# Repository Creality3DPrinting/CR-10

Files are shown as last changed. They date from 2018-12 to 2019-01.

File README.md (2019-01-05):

# CR-10
The original, large build area, all-metal 3D printer from Creality3D is now fully Open Source Hardware Association Certified.

UID:CN000005
https://certification.oshwa.org/list.html

Hardware and software licensed under the GPL v3 license, documentation licensed under CC BY-SA 4.0 International license.

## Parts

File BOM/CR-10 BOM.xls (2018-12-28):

CR-10 BOM
order | Part Code | Part Name | Specification | UNIT | Qty
1 | 400102047 | 2020-L400-X-1 | 20*20-L400 | PCS | 2
2 | 400102015 | 2040-L460-A0-1 | 20*40-L460mm | PCS | 2
3 | 400102048 | 2040-L500-A0-1 | 20*40-L509 | PCS | 1
4 | 400101026 | Y Motor holder 1 | 2.5mmSPCC | PCS | 1
5 | 400205046 | M5X10 Pan Head Screw | M5X10 | PCS | 3
6 | 400202005 | F624 pillow | F624zz | PCS | 4
7 | 400205102 | M5 T-Slot Nut | M5TNUT | PCS | 1
8 | 400205052 | M5X25Socket Head Screw | M5X25 | PCS | 16
9 | 400205107 | M5 Split Washer | M5 | PCS | 1
10 | 200101010 | Hot bed control module |  | PCS | 1
11 | 400101108 | Y Adjustment Block-1 | 2.0mm | PCS | 1
12 | 400408004 | M4X15 Hollow cylinder | 4.2*8*15mm | PCS | 2
13 | 400205012 | M4X50 Sock Head Screw | M4X50 | PCS | 1
14 | 400205137 | M5X30 Socket Head Screw | M5*30 | PCS | 4
15 | 400101025 | Side Plate | 4mmAL5052 | PCS | 1
16 | 400302016 | Hot bed-1 | 310*310*3-220W | PCS | 1
17 | 400505003 | Glass platform | 310*310*4mm | PCS | 1
18 | 400205141 | M4X18-P Flush Head Screw | M4X18-P | PCS | 21
19 | 400205096 | M4 Self-locking nut | M4 | PCS | 1
20 | 400404029 | Y limit switch bracket-1 | 4mm | PCS | 1
21 | 400101016 | Fan holder | 0.8mm | PCS | 1
22 | 400205063 | M3X25-P | M3X25-P | PCS | 4
23 | 400205028 | M3X4 Pan Head Screw | M3*5 | PCS | 9
24 | 400309008 | 4025Fan | 12V-4020-0.12A | PCS | 1
25 | 400305014 | Power supply socket |  | PCS | 1
26 | 200102008 | lcd | 12864 | PCS | 1
27 | 400307001 | lcd Knob |  | PCS | 1
28 | 200101004 | CR-10 Control Panel | Melzi | PCS | 1
29 | 400205134 | M3X18 Combination Screw | M3*18 | PCS | 4
30 | 400205030 | M3X8 Pan Head Screw | M3X8 | PCS | 4
31 | 400309007 | 5010 Fan | 12V-5010-0.12A | PCS | 1
32 | 400205104 | M30 Plastic nut | M30*1.5 | PCS | 2
33 | 400403001 | Support tube | D32-L100 | PCS | 1
34 | 400205088 | M3X6 Hand Twisted Screw | M3*6 | PCS | 2
35 | 400205037 | M4X6 Pan Head Screw | M4X6 | PCS | 4
36 | 400301004 | Power Supply | INPUT:100/220VOUTPUT:12V30A | PCS | 1
37 | 400305013 | Switch |  | PCS | 1
38 | 400102052 | 2040-L550-A0-1 | 20*40-L550 | PCS | 1
39 | 400102064 | 2040-L550-A0-1 | 20*40-L550 | PCS | 1
40 | 400201001 | 42-34 motor | JK42HS34-0844YA-03F | PCS | 1
41 | 400402010 | Z motor bracket |  | PCS | 1
42 | 400208001 | Z coupler | CI-20X26-5X8 | PCS | 1
43 | 400205140 | M3X40-P | M3X10-P | PCS | 4
44 | 400102020 | 2020-L400-A0-1 | 20*20-L400mm | PCS | 1
45 | 400102054 | 2020-L415-A0-1 | 20*20-L415mm | PCS | 1
46 | 400101029 | Fan cover | 0.8mmSPOCC | PCS | 1
47 | 400309005 | Nozzle fan | 12V-4010-0.07A-L1200-N5800 | PCS | 1
48 | 400309006 | Cold section fan | 12V-4010-0.2A，L1200 | PCS | 1
49 | 400402023 | Nozzle fan duct |  | PCS | 1
50 | 400205002 | M2X8 Socket Head Screw | M2X8 | PCS | 2
51 | 400205003 | M2X10 Socket Head Screw | M2X10 | PCS | 2
52 | 400101027 | Z Stent | 3.0mm | PCS | 1
53 | 400402021 | Z Threaded Rod Holder-A |  | PCS | 1
54 | 400402022 | Z Threaded Rod Holder-B |  | PCS | 1
55 | 400205042 | M4X20 Pan Head Screw | M4X20 | PCS | 2
56 | 400205061 | M3X14 Flush Head Screw | M3*14-P | PCS | 2
57 | 400101006 | X Adjustment Block | 3mm | PCS | 1
58 | 400205057 | M8X25 Pan Head Screw | M8X25 | PCS | 1
59 | 400205093 | M8 nut | M8Nut | PCS | 1
60 | 400202003 | F688 pillow | F688 | PCS | 3
61 | 400205098 | M8 Self-locking nut | M8Nut | PCS | 1
62 | 400205013 | M4X8 Socket Head Screw | M4X8 | PCS | 3
63 | 400205101 | M4 T-Slot Nut | M4TNut | PCS | 5
64 | 400101103 | E motor bracket | 2.5mmAL5052 | PCS | 1
65 | 400101104 | X motor bracket | 3mmAL5052 | PCS | 1
66 | 400205055 | M5X40 Pan Head Screw | M5X40 | PCS | 3
67 | 400108001 | Spacers for rollers | D8-d5-H-8.35mm | PCS | 12
68 | 400403003 | Rollers | D16 | PCS | 15
69 | 400205110 | M5 washer1 | M5*8*1 | PCS | 15
70 | 400202004 | 625pillow | 625 | PCS | 30
71 | 400205097 | M5 Self-locking nut | M5Nut | PCS | 15
72 | 400201004 | 40-42 motor | JK42HS40-1004AC-01F | PCS | 3
73 | 400402027 | E housing |  | PCS | 1
74 | 400205031 | M3X10 Pan Head Screw | M3X10 | PCS | 8
75 | 400205060 | M3X10 Flush Head Screw | M3X10-P | PCS | 1
76 | 400402026 | E idler tensioner |  | PCS | 1
77 | 400205007 | M3X18 Socket Head Screw | M3X18 | PCS | 1
78 | 400202002 | 624U pillow | 624U | PCS | 1
79 | 400205111 | z nut | T8*8 | PCS | 1
80 | 400205106 | M4 Split Washer | M4 | PCS | 5
81 | 400205105 | M3 Split Washer | M3 | PCS | 6
82 | 400304001 | limit switch | 3PIN | PCS | 3
83 | 400103001 | E gear | D11-40 | PCS | 1
84 | 400204002 | Extrusion Spring | 1.1*外8*L22 | PCS | 1
85 | 400210002 | M6 Pneumatic joint | KJH04-06 | PCS | 1
86 | 400211001 | 2GT-pulley | 2GT-d5-20-6mm | PCS | 2
87 | 400404038 | X limit switch bracket |  | PCS | 1
88 | 400205029 | M3X6Pan Head Screw | M3X6 | PCS | 18
89 | 400108002 | Eccentric column | D7.2-d5-H-8.35mm | PCS | 6
90 | 400202148 | M4X16 Pan Head Screw | M4X16 | PCS | 2
91 | 400101002 | E plate | 2.5mmAL5052 | PCS | 1
92 | 400205053 | M5X30 Pan Head Screw | M5X30 | PCS | 12
93 | 400205109 | M5 washer | M5 | PCS | 5
94 | 400205041 | M4X16 Pan Head Screw | M4X16 | PCS | 2
95 | 400205015 | M4X16 Screw | M4*16 | PCS | 2
96 | 400105008 | Radiator | 12*20*27.8mm,2*M3 | PCS | 1
97 | 400107006 | Catheter | D7*M6-L27mm | PCS | 1
98 | 400104004 | Heat block | 20*20*10 | PCS | 1
99 | 400106003 | nozzle | D6-0.4mm | PCS | 1
100 | 400205018 | M3 Screw | M3X3 | PCS | 2
101 | 400308005 | Heater | 12V，40W-L1200mm，Φ6*20 | PCS | 1
102 | 400303008 | Nozzle thermistor | D1.8-L1200mm-100K | PCS | 1
103 | 400205021 | M3X4 Screw | M3X4 | PCS | 1
104 | 400210001 | Pneumatic joint | D4M8 | PCS | 1
105 | 400407003 | D4 Teflon tube | D4-d2-L440mm | PCS | 1
106 | 400205007 | M3×18 Flush Head Screw | M3×25 | PCS | 2
107 | 400205032 | M3X16 Pan Head Screw | M3X16 | PCS | 4
108 | 400204001 | Bed level springs | 0.9*8*L17 | PCS | 4
109 | 400205066 | M4X30 Flush Head Screw | M4*30-P | PCS | 4
110 | 400205164 | Hand Twisted Nut | M4-D60 | PCS | 4
111 | 400402020 | 2020 Endcap | 2020 | PCS | 6
112 | 400404035 | Connecting Block | 40*55*5 | PCS | 4
113 | 400406005 | Foot Cushion | D25*3mm | PCS | 4
114 | 400205039 | M4X10 Pan Head Screw | M4X10 | PCS | 1
115 | 400101030 | Casing | 0.8mmSPCC | PCS | 1
116 | 400101032 | Sipport Frame1 | 1.5mmSPCC | PCS | 1
117 | 400101127 | Bottom cover | 0.8mmSPCC | PCS | 1
118 | 400404037 | T-jiont plates | 5mm | PCS | 1
119 | 400404036 | T-jiont plates | 5mm | PCS | 1
120 | 400206001 | Z threaded rod-514 | D8-T8*8-L515mm | PCS | 1
121 | 400205015 | M4X16 Sochet Head Screw | M4*16 | PCS | 1
122 | 400306225 | Y Motor Line | L420mm | PCS | 1
123 | 400306226 | Z Motor Line | Motor LineL280mm，Limit Line L180mm | PCS | 1
124 | 400306069 | Display line | 10pin,L190mm | PCS | 1
125 | 400306121 | power line | 16#-L200mm,XT60 | PCS | 1
126 | 400306124 | Red silicone wire | 16#-L200mm | PCS | 1
127 | 400306125 | Red silicone wire | 16#-L150mm | PCS | 1
128 | 400306127 | Red silicone wire | 16#-L170mm | PCS | 1
129 | 400306128 | Yellow silicone wire | 18#-L170mm | PCS | 1
130 | 400306144 | Black silicone wire | 16#-L200mm | PCS | 1
131 | 400306145 | Black silicone wire | 16#-L170mm | PCS | 1
132 | 400306147 | Red silicone wire | 16#-L100mm | PCS | 1
133 | 400306148 | Black silicone wire | 16#-L100mm | PCS | 1
134 | 400306151 | X,E Motor Line | Motor Line L860mm、980mm，Limit Line L920mm | PCS | 1
135 | 400306152 | Y Motor Line | Motor Line L860mm，Limit Line L780mm | PCS | 1
136 | 400306153 | Z Motor Line | Motor Line L860mm，Limit Line L780mm | PCS | 1
137 | 400306234 | aviation connector-8 |  | PCS | 1
138 | 400306235 | aviation connector-8 |  | PCS | 1

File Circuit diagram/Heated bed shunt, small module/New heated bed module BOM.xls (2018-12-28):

 | 新热床模块BOM单
序号 | 名称 | 物料规格 | 位置 | 封装 | 单位 | 单位用量
1 | 连接器 | 2PIN 2.54间距米色座子 | Control In | XH2.54-2A | PCS | 1
2 | LED | 蓝色LED灯 | D1, D2 | 0805 | PCS | 2
3 | 场效应管 | HA210N10 | Q2 | TO-247 | PCS | 1
4 | 电阻 | 2K ±1% 1/8W | R1, R3 | 0805 | PCS | 2
5 | 电阻 | 10K ±1% 1/8W | R2, R4, R5 | 0805 | PCS | 3
6 | 整流桥堆 | MP6S 整流桥堆 600V/0.5A | U1 | SOP-4 | PCS | 1
7 | 连接器 | 7.62mm间距 3PIN 连接器 | U2 | KF7.62-3P | PCS | 1
8 | 光电耦合器 | PC817 光电耦合器 | U3 | SOP-4 | PCS | 1

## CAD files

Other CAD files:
3D/CR-10.sldasm
3D/CR-10_1.sldasm
2D/E motor bracket.dwg
2D/Fan holder.DWG
2D/Rollers.dwg
2D/Z Threaded Rod Holder-A.DWG
2D/Support Frame.DWG
2D/Bottom cover.DWG
2D/Glass platform.DWG
2D/Y limit switch bracket.DWG
2D/2040-L460-A0-1.DWG
2D/X limit switch bracket.DWG
2D/Heat block.dwg
2D/2020-L415-A0-1.DWG
2D/Y Motor holder.DWG
2D/E housing.dwg
2D/Y Adjustment Block.DWG
2D/Fan cover.dwg
2D/2020 Endcap.dwg
2D/2020-L400-A0-1.DWG
2D/2040-L500-A0-1.DWG
2D/Casing.DWG
2D/Catheter.dwg
2D/E idler tensioner.dwg
2D/E plate.dwg
2D/Eccentric column.dwg
2D/Foot Cushion.DWG
2D/Hand Twisted Nut.dwg
2D/M30 Plastic nut.dwg
2D/Nozzle fan duct.dwg
2D/Radiator.dwg
2D/Side Plate.DWG
2D/Spacers for rollers.dwg
2D/Support tube.dwg
2D/T-jiont plates-2.DWG
2D/T-jiont plates.DWG
2D/X Adjustment Block.dwg
2D/X motor bracket.dwg
2D/Z Stent.dwg
2D/Z Threaded Rod Holder-B.DWG
2D/Z motor bracket.dwg
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

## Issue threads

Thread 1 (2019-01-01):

CR-10 Schematic.pdf does not match CR-10 Motherboard.PCB

RudolphRiedel, 2019-01-01:
Thank you for making all this available!
I just found out about it, this would probably have stopped me from doing my own version.

But the provided CR-10 Schematic.pdf does not match CR-10 Motherboard.PCB.
The part names are all wrong, the controller is named U5 in your schematic but named U8 on the board.
I have not found a single part yet that has the same name in your CR-10 Schematic.pdf  as in your CR-10 Motherboard.PCB.
Also the values for the components do not match and some values are even missing.
And some of the signal names to do not match as well.

Please do provide a schematic that matches the board file.
And please do consider providing the schematic in binary form as well as placement plan in .pdf for the board.

RudolphRiedel, 2019-01-12:
The header J5 clearly shows that the provided "CR-10 Schematic.pdf" is not for the V1.1.2 version of the board but for the earlier revision that did not have a revision printed on the silkscreen.
The V1.1.2 board does not have the jumper to switch 5V from VREG_5V to USB.

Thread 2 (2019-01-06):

Values missing for components in Power section of the Schematics

CurtisLeeBolin, 2019-01-06:
Circuit diagram/Motherboard/CR-10 Schematic.pdf

In the Power section, I only see a value for the integrated circuit, an inductor, and the fuse.  No values are given for the other components.  Also the inductor is not numbered.  It is still labeled "L?".

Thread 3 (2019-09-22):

Missing files for electrical components

spermman, 2019-09-22:
I saw a post that made it sound like at one time the models for the board, power supply and display were available.

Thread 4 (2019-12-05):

CR-20 Files and 3D Assembly

amv101, 2019-12-05:
Thanks for making these files available! Great work!

Any chance we can get CR-20 / CR-20 Pro 3D Assembly and PCB schematic files? It seems it is almost identical to the Ender 3, with the exception of the bottom frame housing and mainboard parts.

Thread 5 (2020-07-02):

8-Pin Aviation connector Pinout is incorrect

edumaker-limited, 2020-07-02:
Hi, here is an erratum for the file:
400306234-aviation connector-8-Model.pdf

The PDF states:
1. 1#2# Heater
2. 3#4# Nozzle thermistor
3. 5#nozzle fan (rad), 6#nozzle fan (black)
4. 7#cold section fan(rad); 8#cold section fan(blac).

This is incorrect - the fans are swapped around.  My source:  I own 15 CR10 variants from original to 10s to 10S5, all are the same, and do not match this document.

Here is a suggested correction including spelling and more commonly heard English terminology for the parts:

1. 1#2# Heater
2. 3#4# Nozzle thermistor
3. 5# Heat-sink fan (red); 6#Heat-sink fan (black)
4. 5# part cooling fan (red); 6# part cooling fan (black)

Kind regards,
Alex Gibson
Edumaker Limited

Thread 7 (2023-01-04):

missing Data: X-Carriage & Hotend-Assembly of CR-10 V2 Version

ij0n, 2023-01-04:
I have a CR10-V2. The X-Carriage and Hotend-Assembly does not match the data provided here. I have furthermore added a BL-Touch to that setup. I'd like to have the 3D-Data to design additional attachments for the X-Carriage.

Can you please upload that data?

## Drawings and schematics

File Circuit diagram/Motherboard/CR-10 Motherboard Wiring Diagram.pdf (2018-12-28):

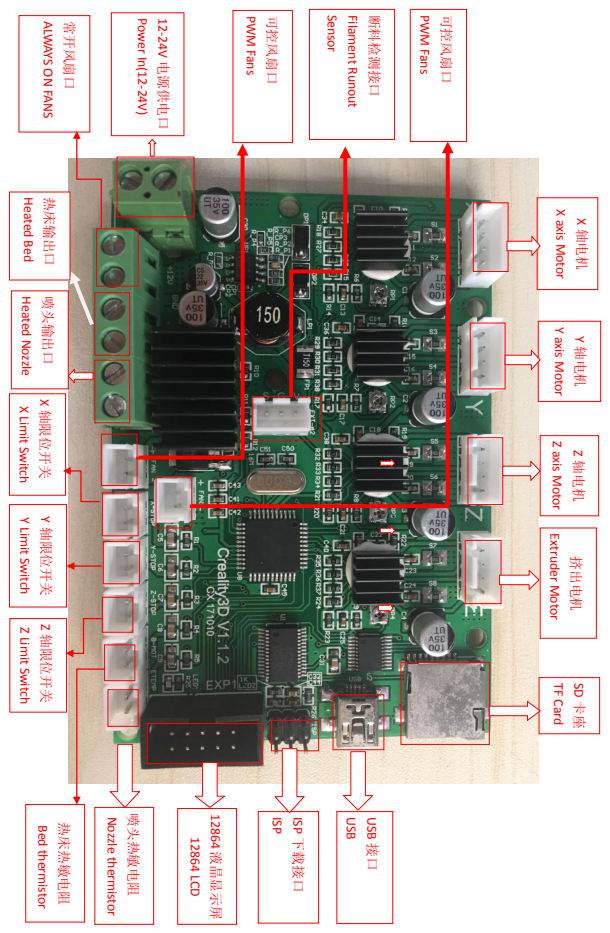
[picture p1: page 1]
Z 轴限位开关; Z Limit Switch; Y 轴限位开关; Y Limit Switch; Z 轴电机; Z axis Motor; USB; 12-24V 电源供电口; Power In(12-24V); 热床输出口; 喷头输出口; Nozzle; PWM; 可控风扇口; Fans; 常开风扇口; 喷头热敏电阻; thermistor; 热床热敏电阻; Bed thermistor; 12864液晶显示屏; 12864 LCD; 轴限位开关 Y 轴限位开关; X Limit Switch; 轴限位开关; Y 轴电机; Y axis Motor; 挤出电机; Extruder Motor; ISP 下载接口; ISP; Filament; 断料检测接口; Runout; Sensor

ALWAYS ON FANS

eated Bed Heated

X Z X 轴电机 X axis Motor SD 卡座 TF Card USB 接口

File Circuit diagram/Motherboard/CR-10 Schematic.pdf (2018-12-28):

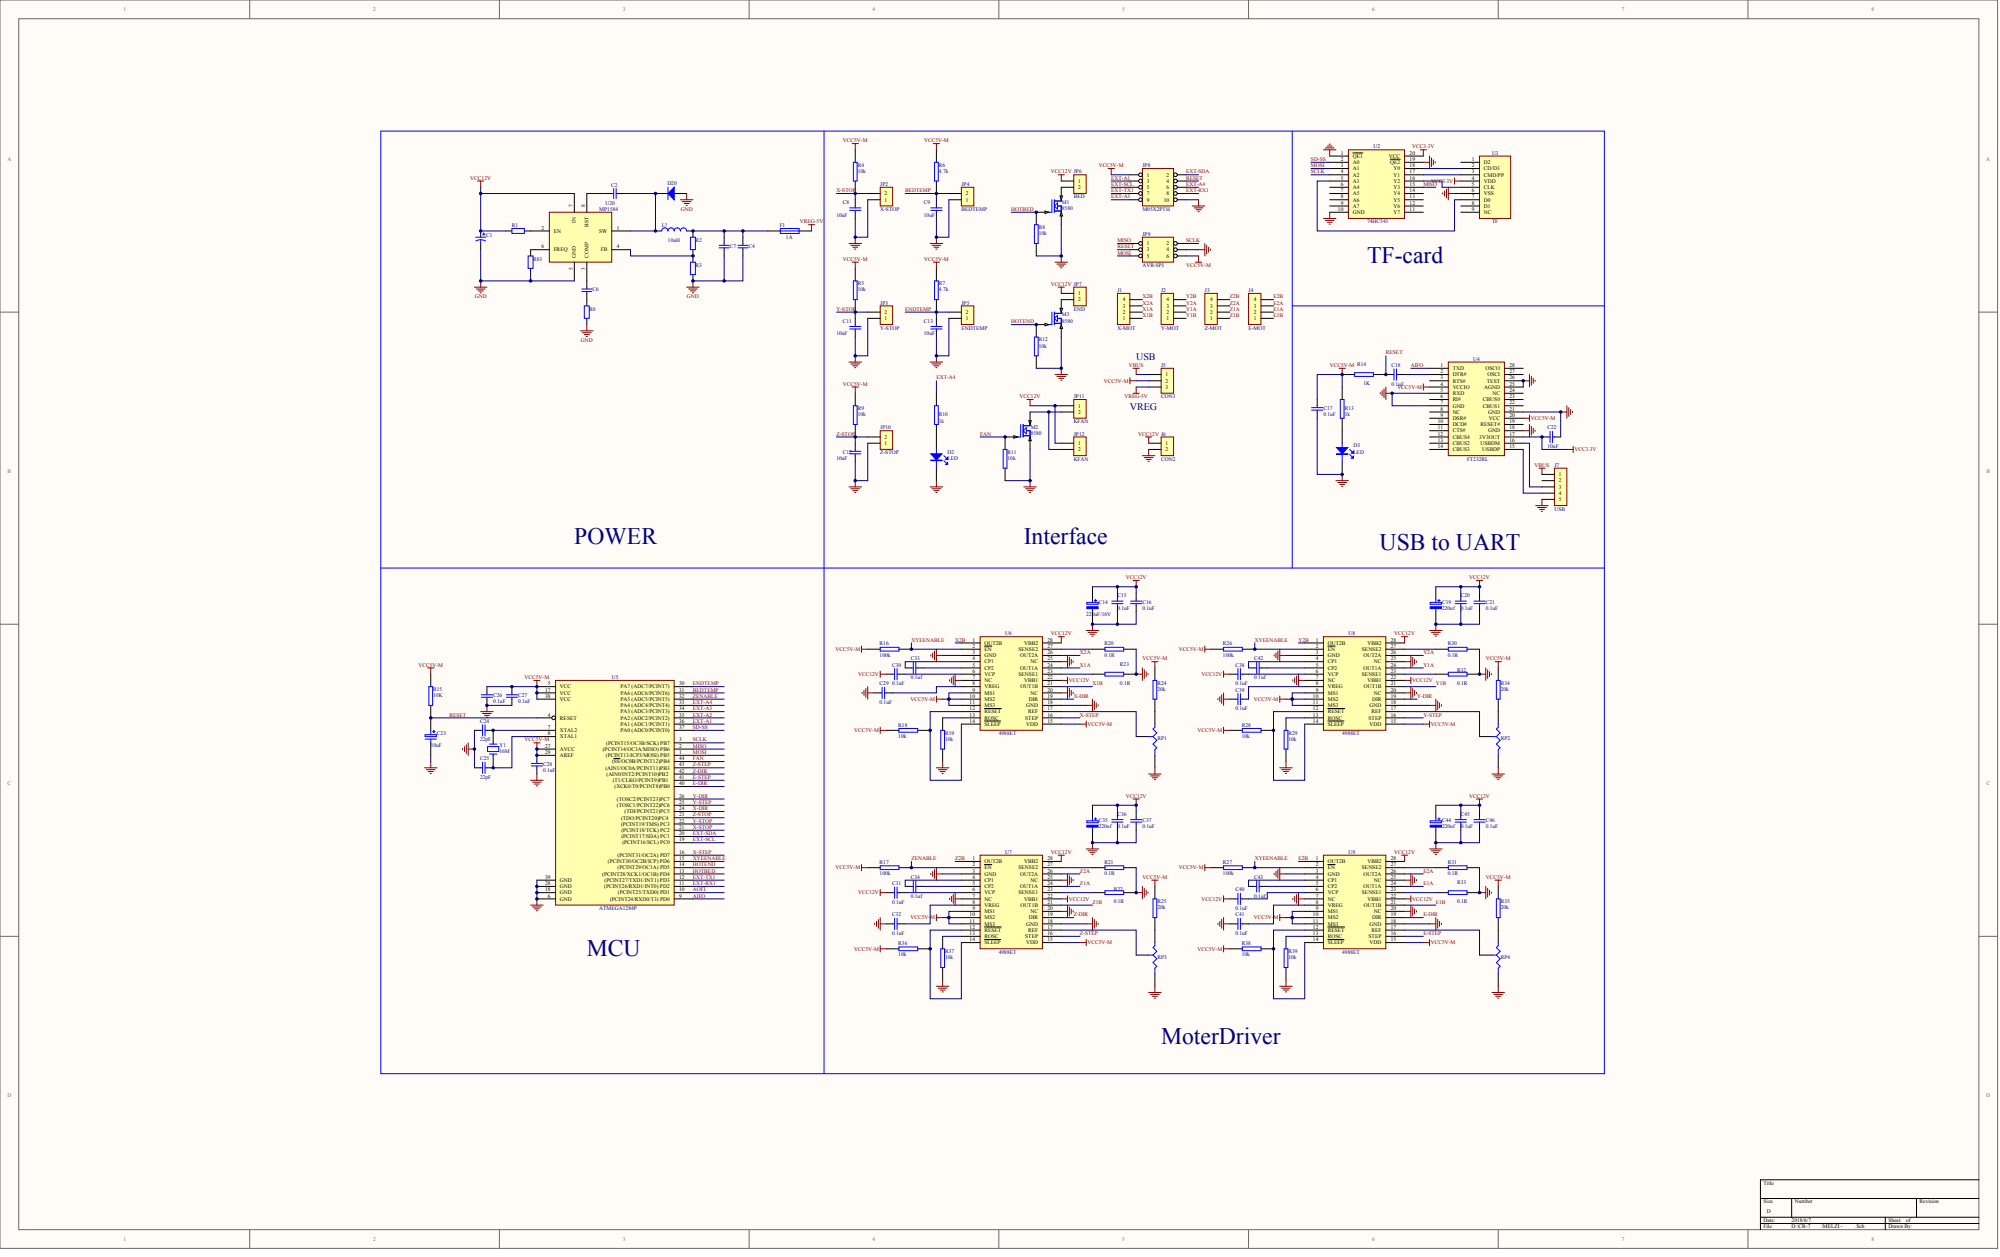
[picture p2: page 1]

DCD# 10 P0U4019 P0U4019 P0U4019
CTS# 11 | P0U4018 P0U4018 P0U4018

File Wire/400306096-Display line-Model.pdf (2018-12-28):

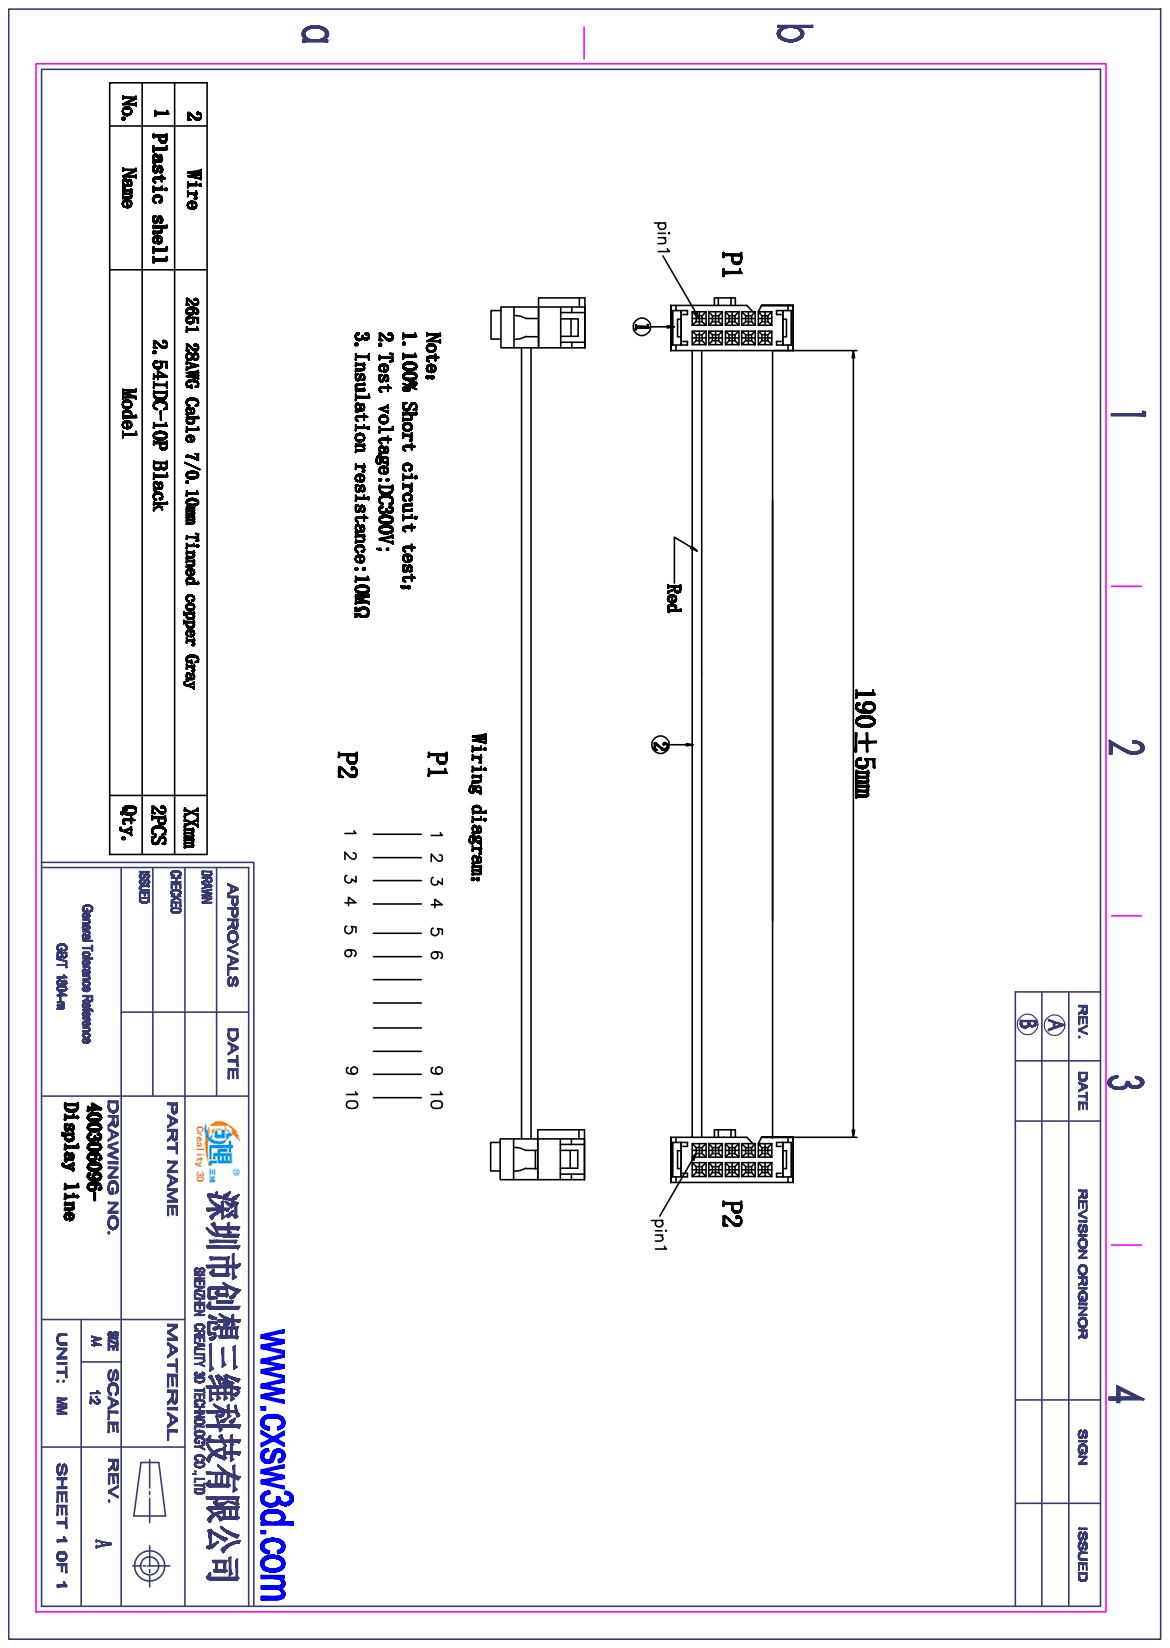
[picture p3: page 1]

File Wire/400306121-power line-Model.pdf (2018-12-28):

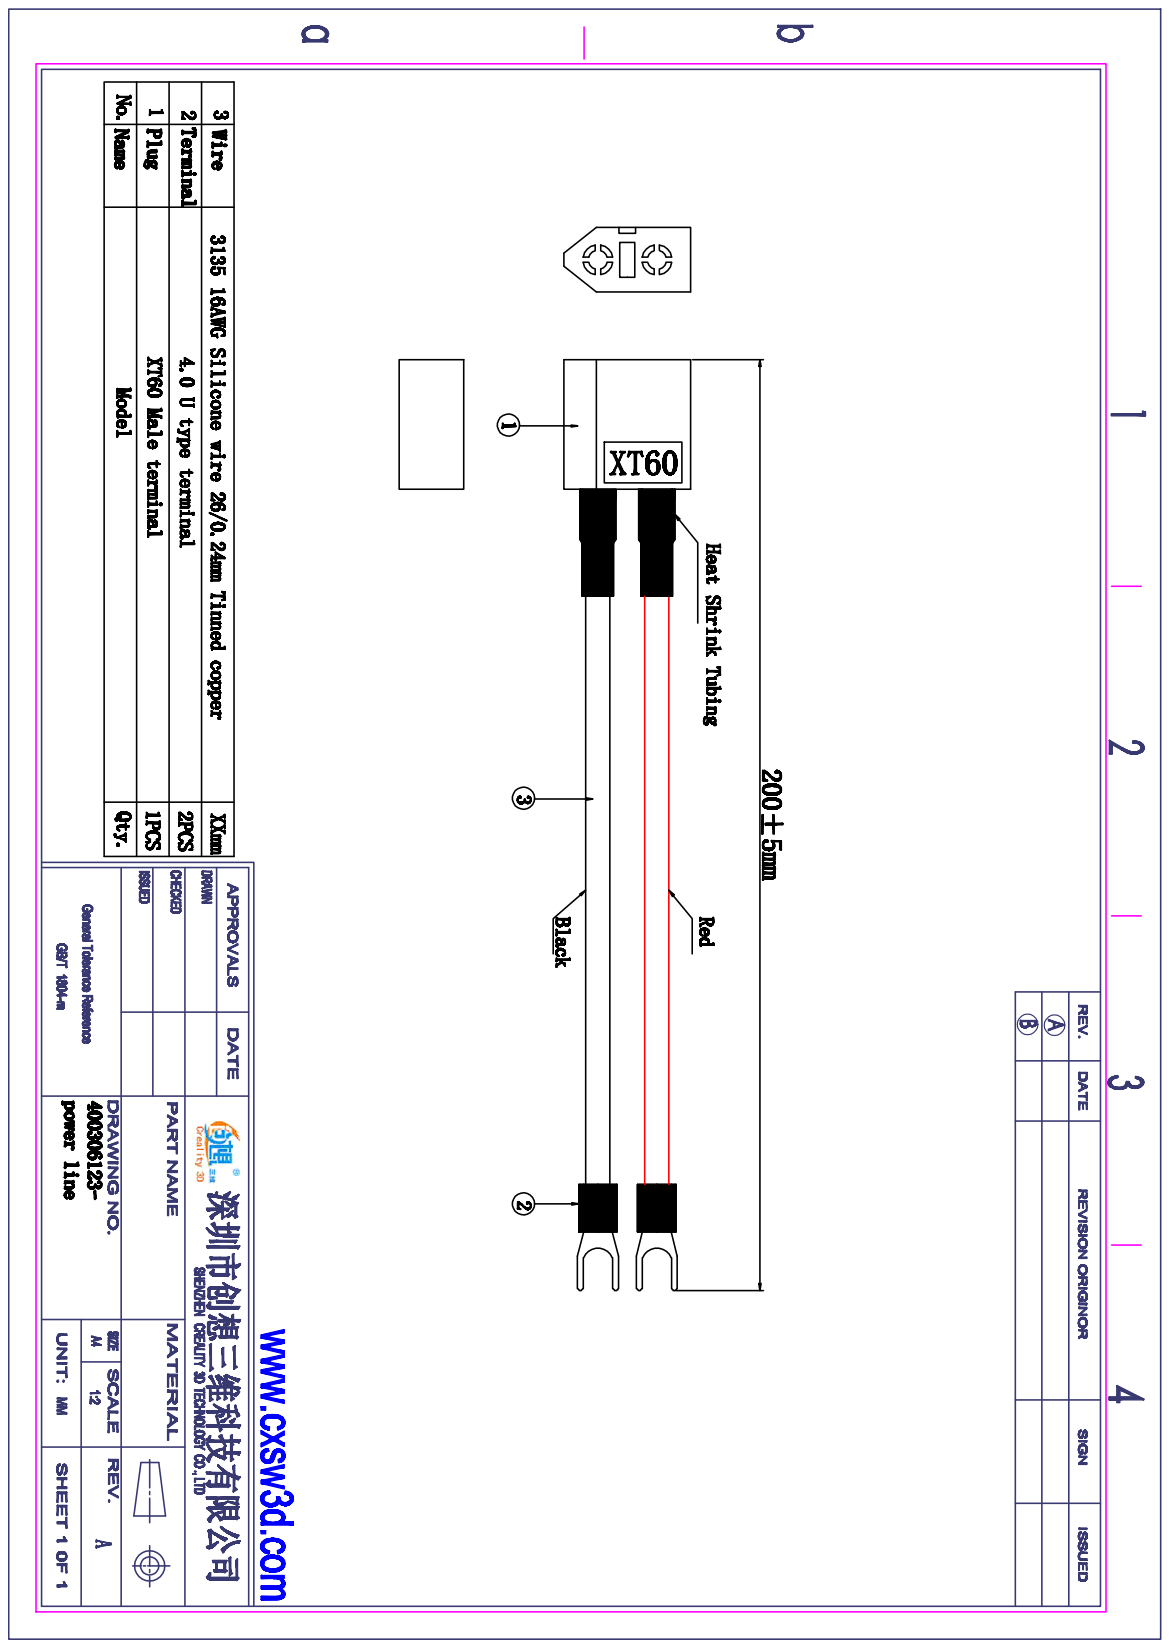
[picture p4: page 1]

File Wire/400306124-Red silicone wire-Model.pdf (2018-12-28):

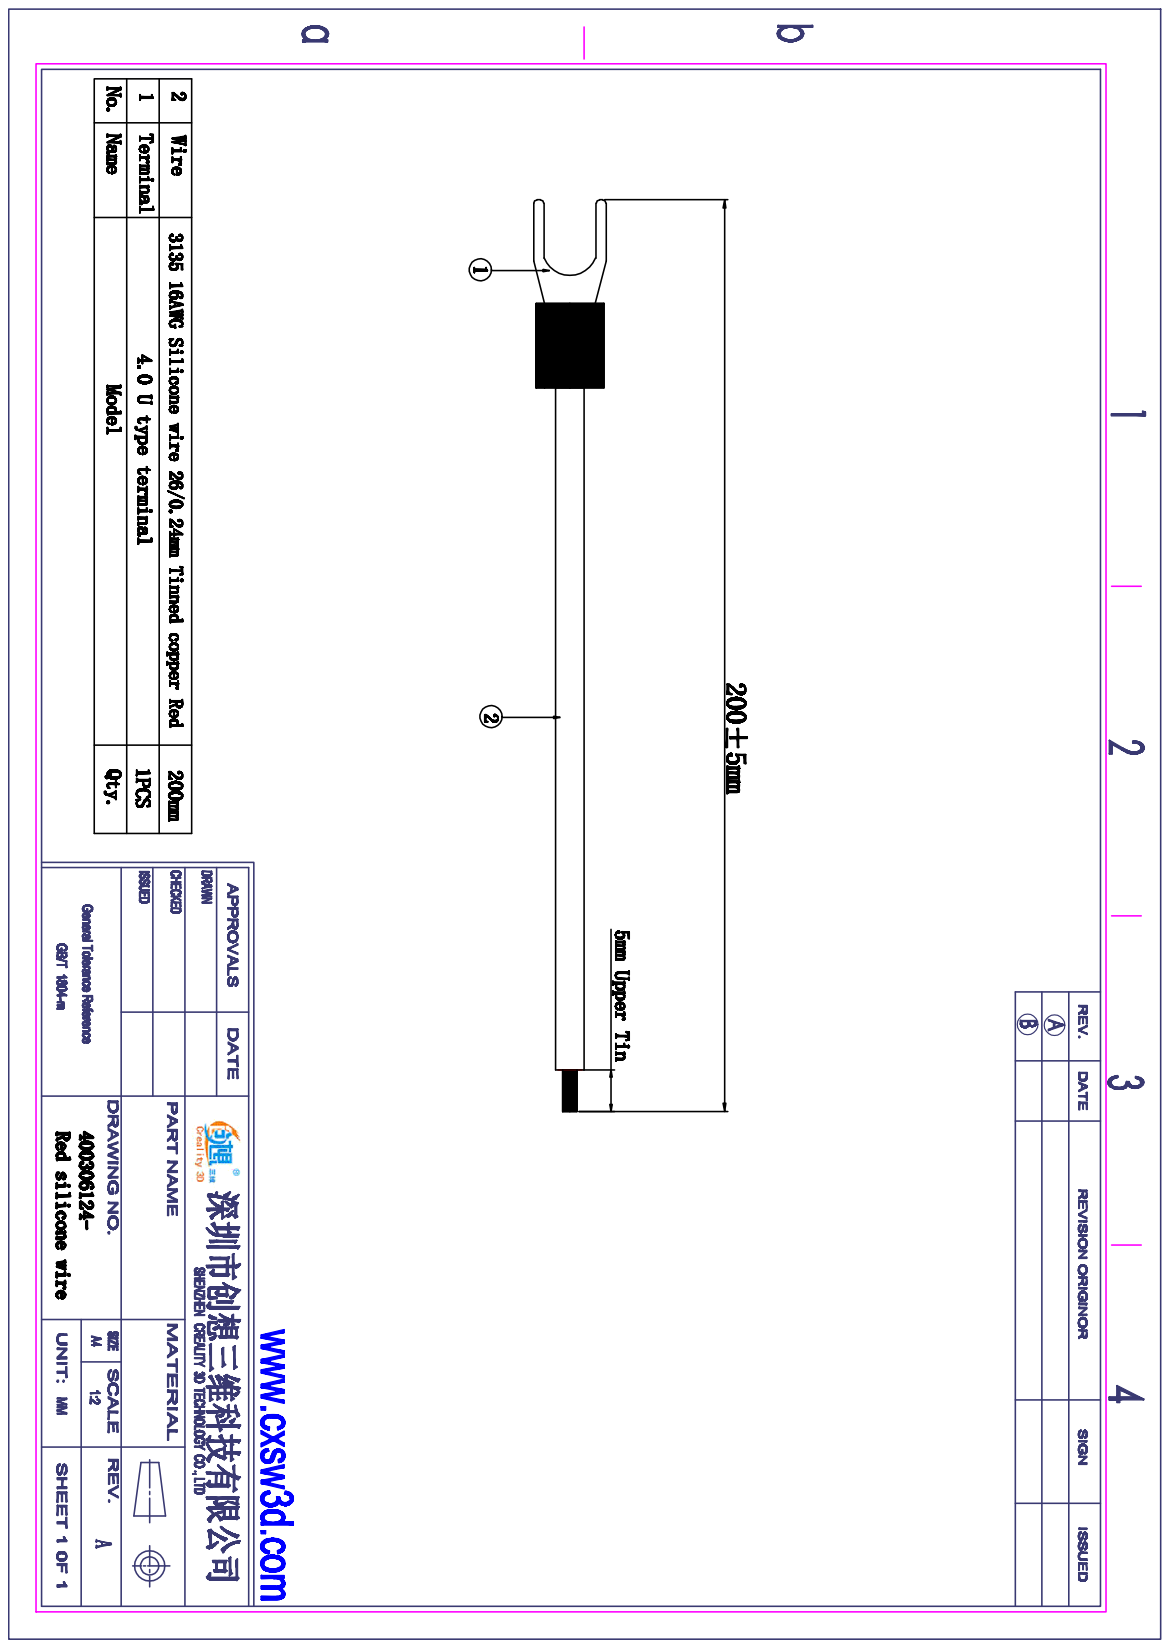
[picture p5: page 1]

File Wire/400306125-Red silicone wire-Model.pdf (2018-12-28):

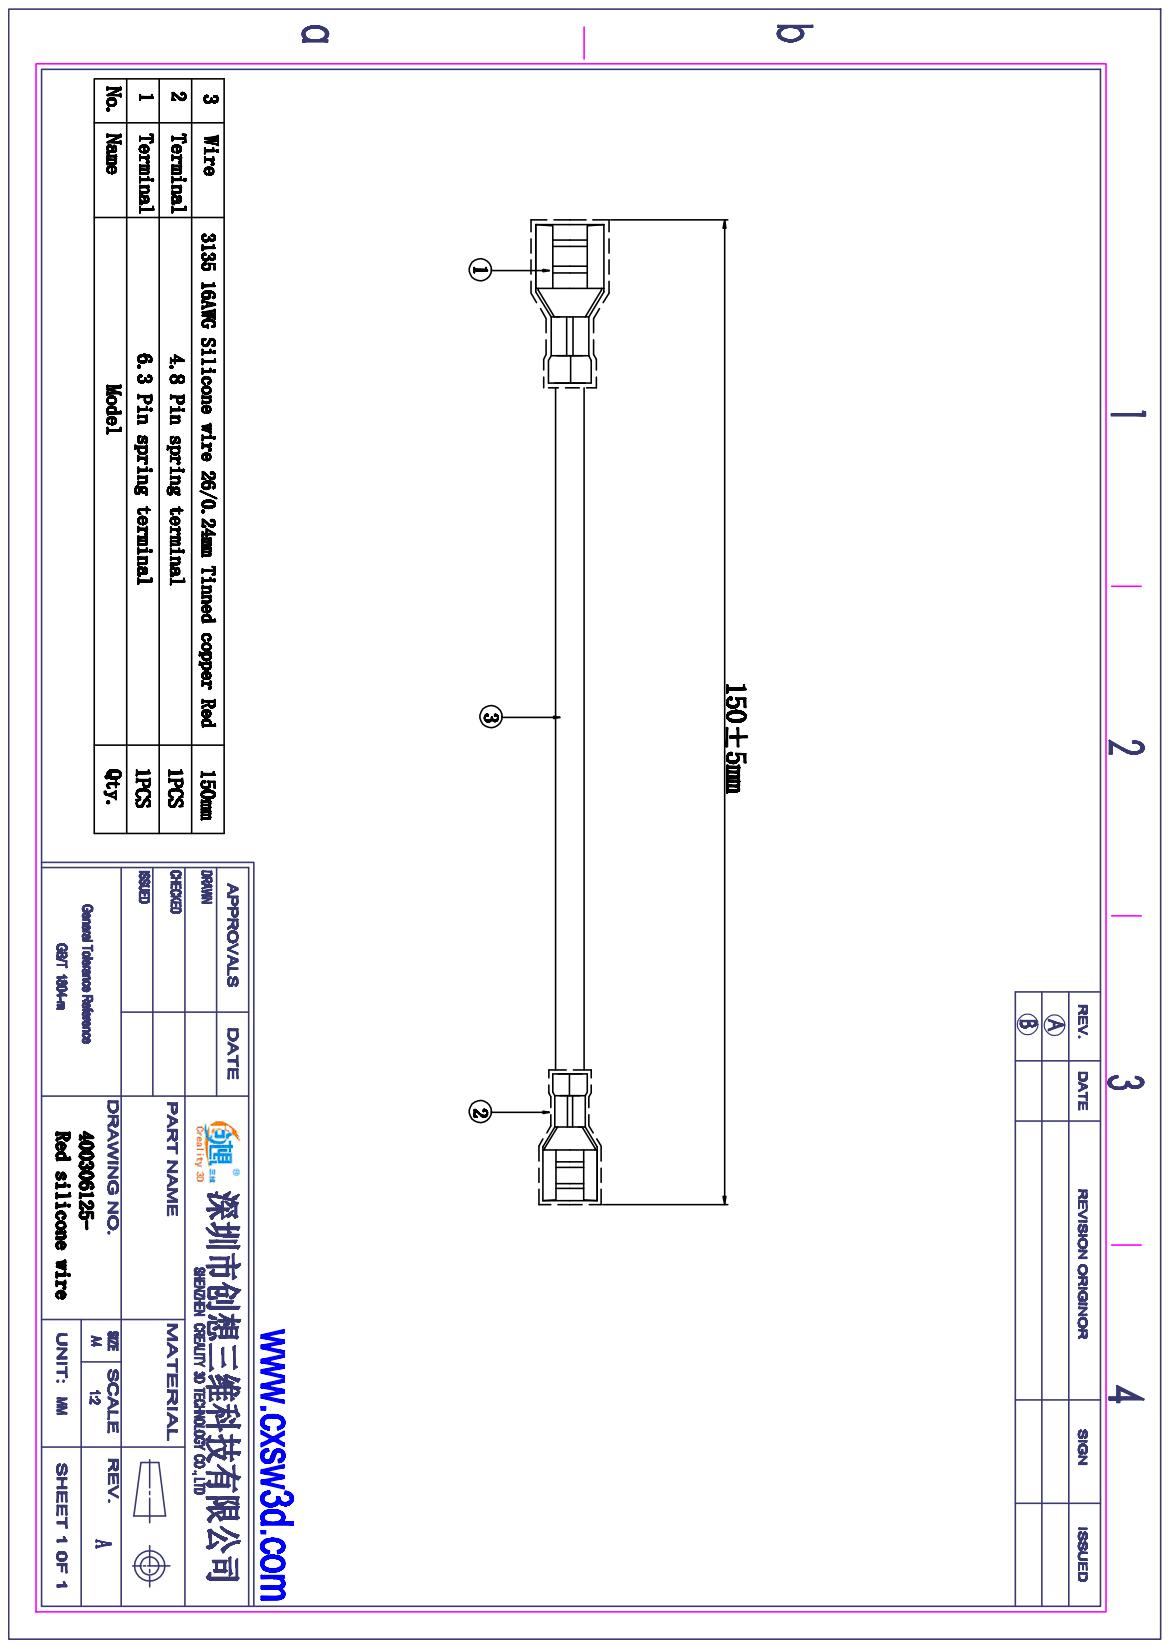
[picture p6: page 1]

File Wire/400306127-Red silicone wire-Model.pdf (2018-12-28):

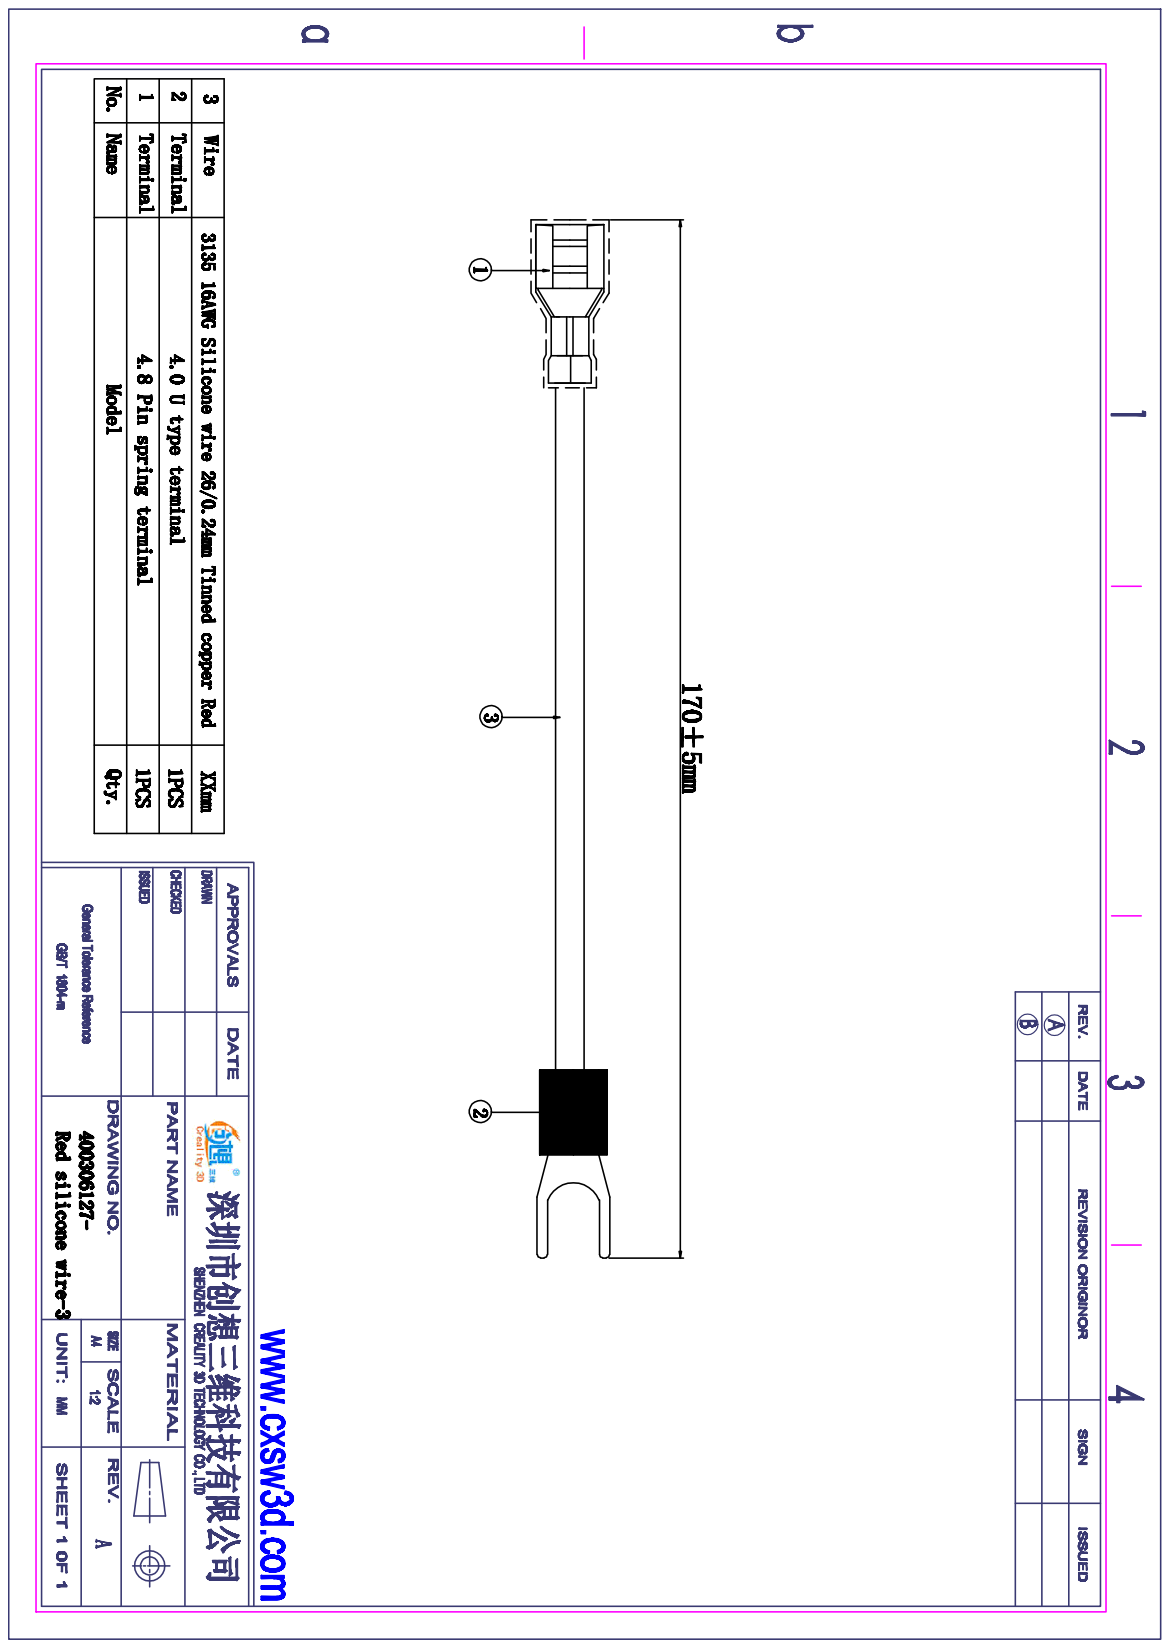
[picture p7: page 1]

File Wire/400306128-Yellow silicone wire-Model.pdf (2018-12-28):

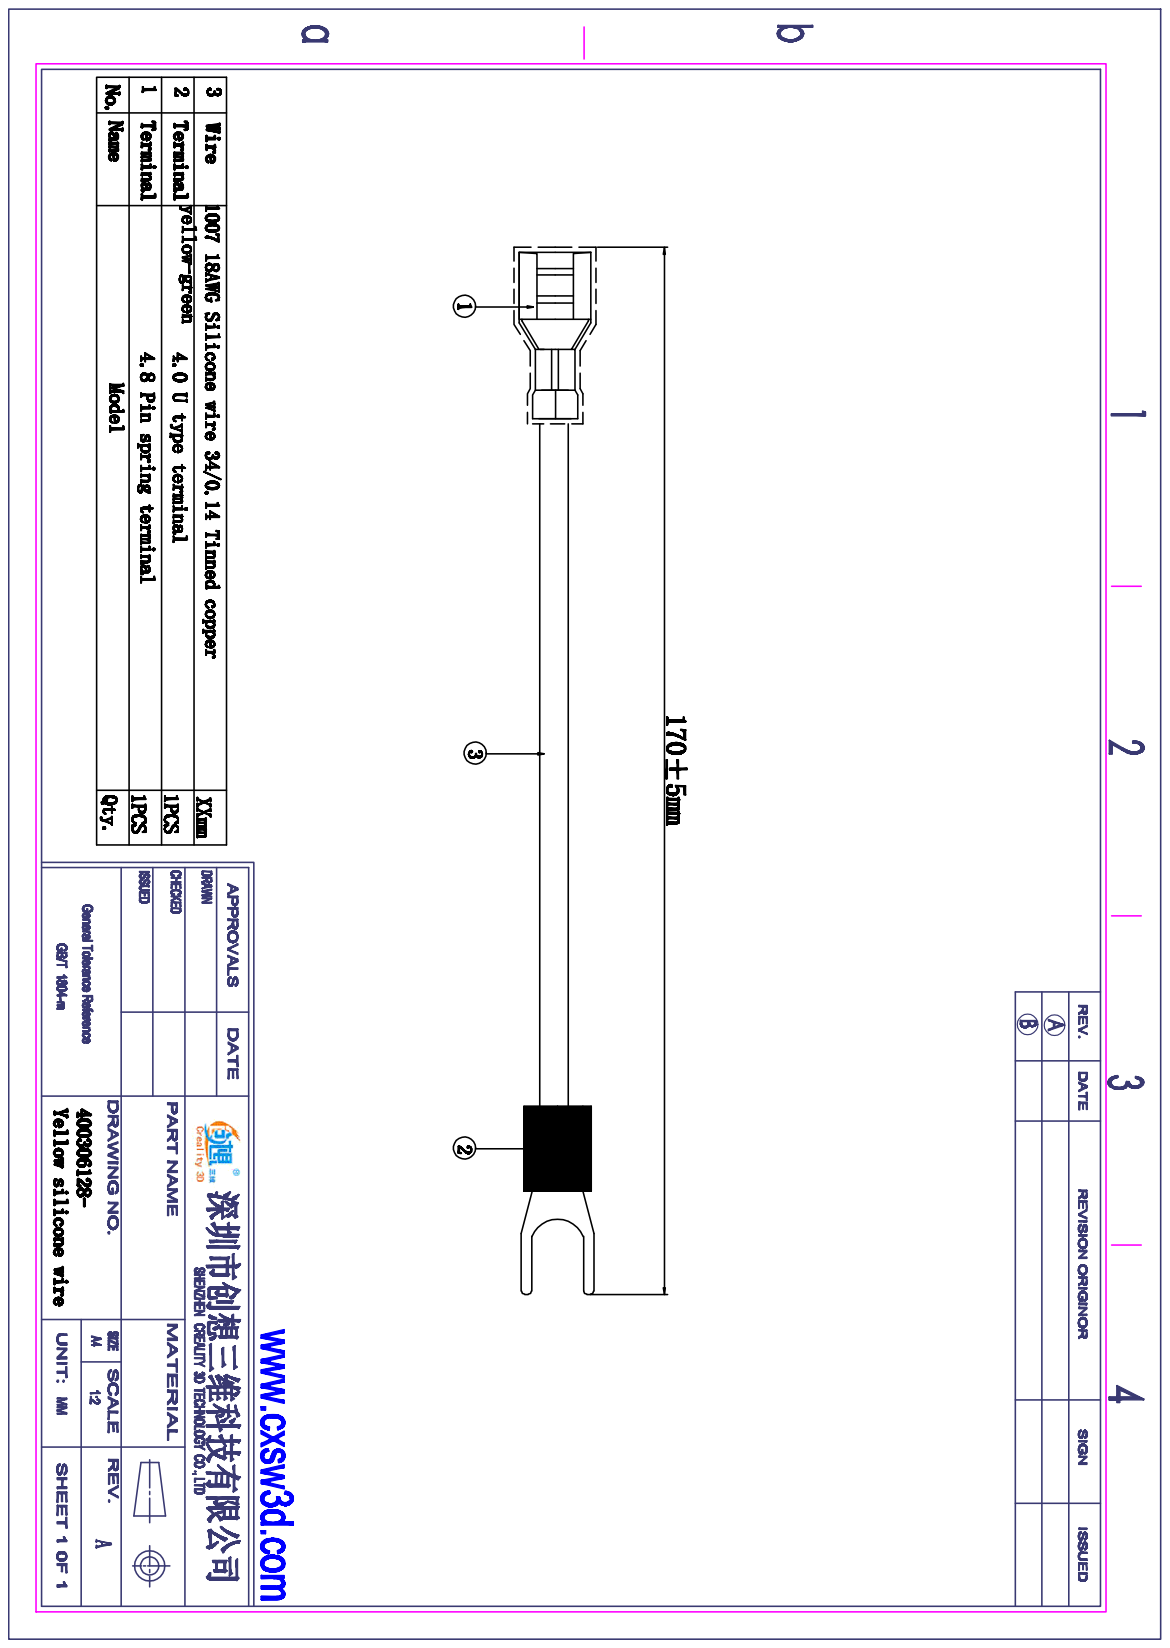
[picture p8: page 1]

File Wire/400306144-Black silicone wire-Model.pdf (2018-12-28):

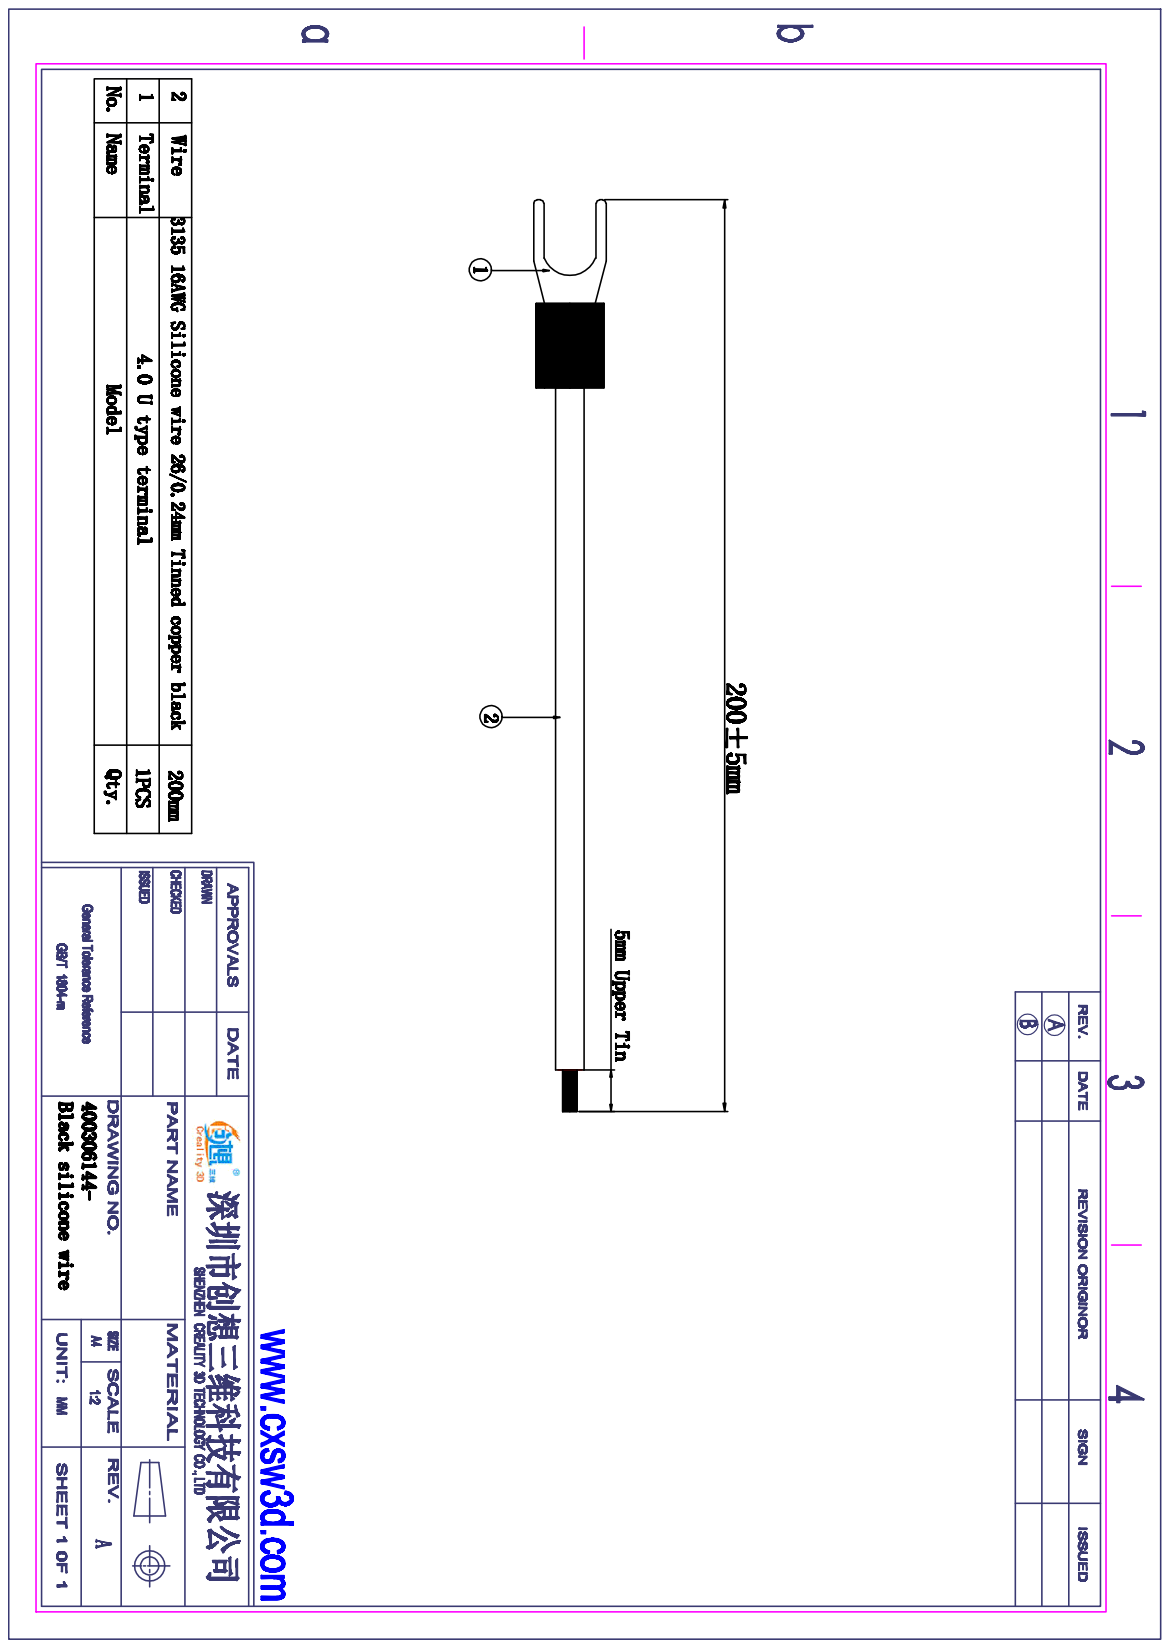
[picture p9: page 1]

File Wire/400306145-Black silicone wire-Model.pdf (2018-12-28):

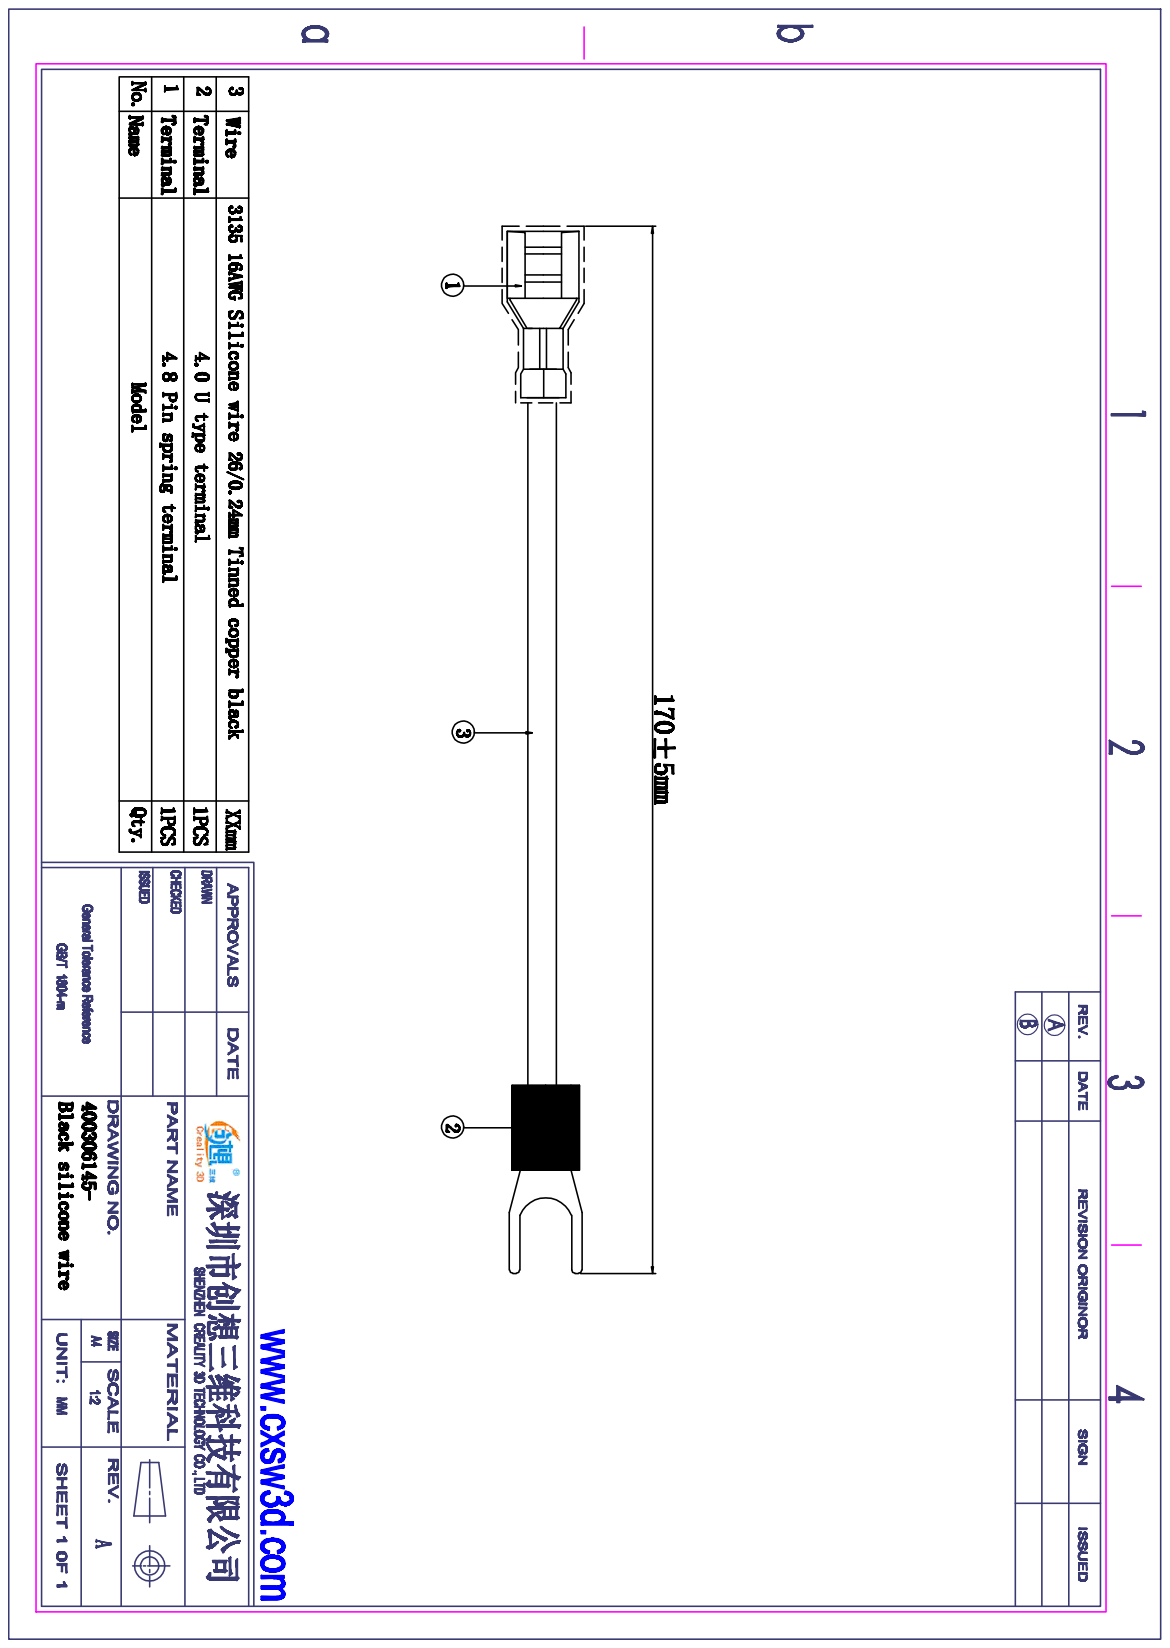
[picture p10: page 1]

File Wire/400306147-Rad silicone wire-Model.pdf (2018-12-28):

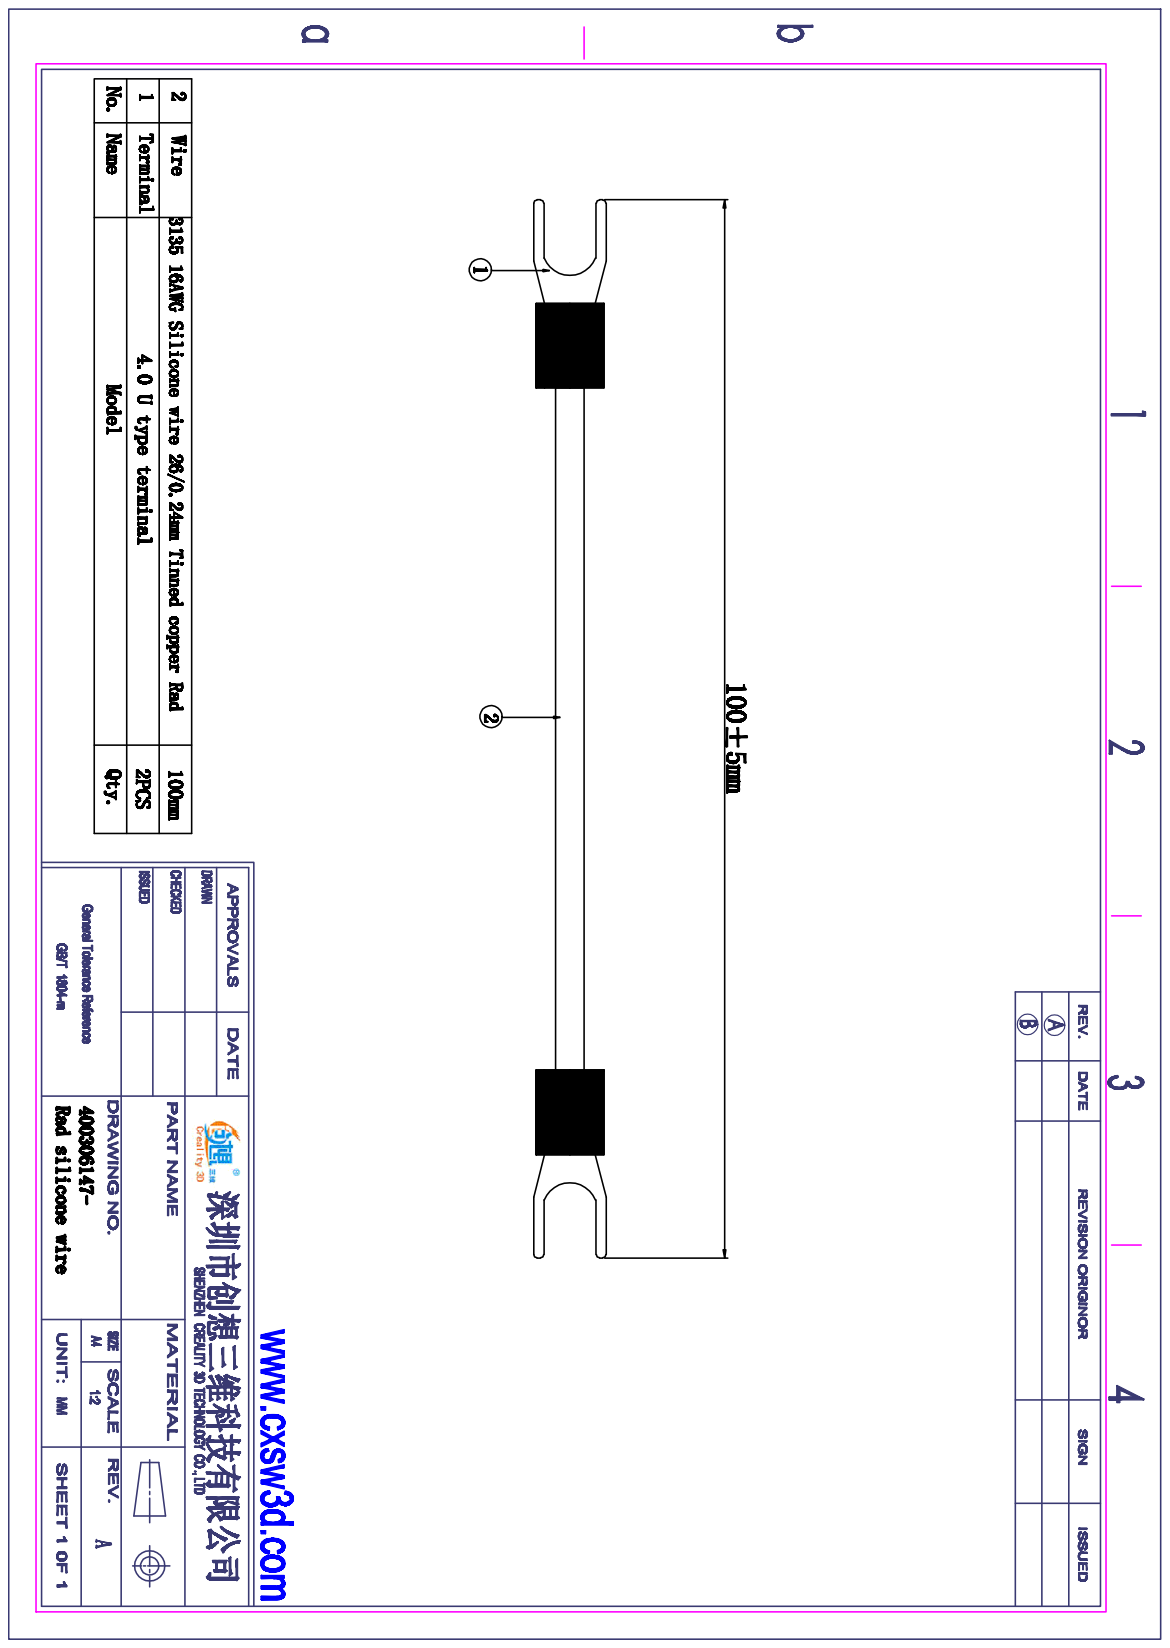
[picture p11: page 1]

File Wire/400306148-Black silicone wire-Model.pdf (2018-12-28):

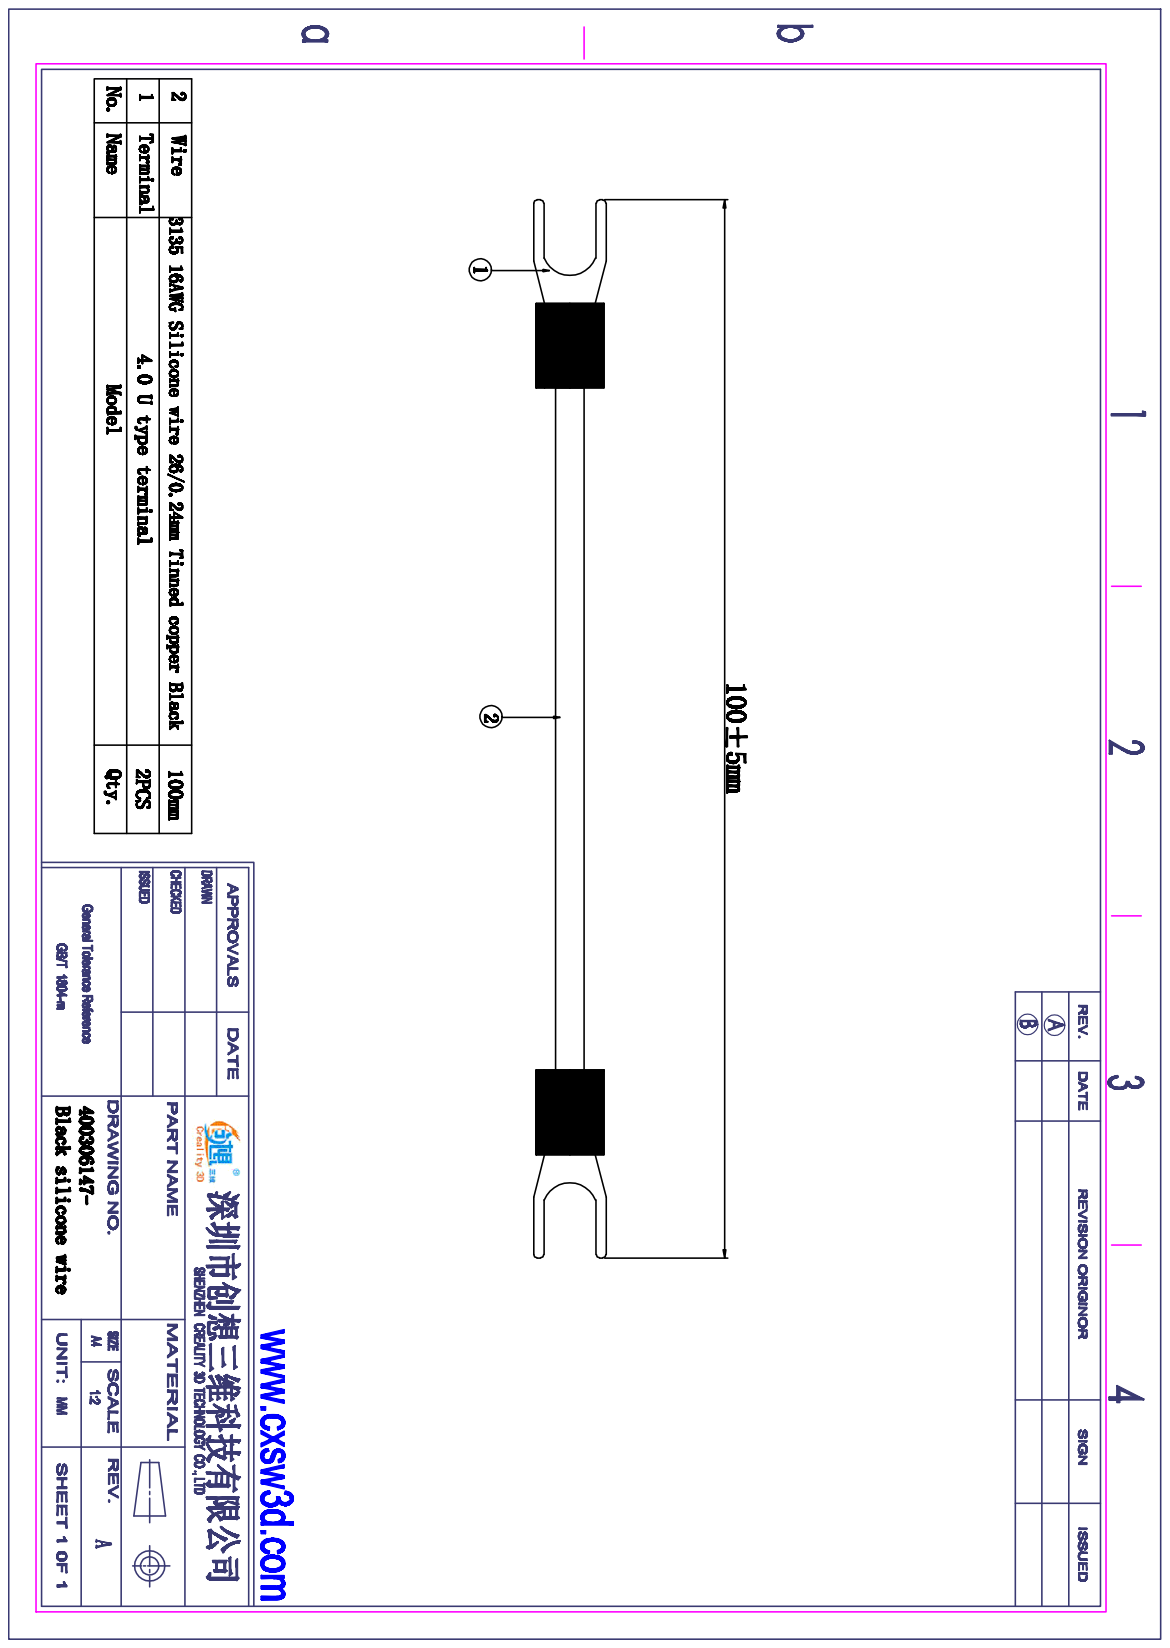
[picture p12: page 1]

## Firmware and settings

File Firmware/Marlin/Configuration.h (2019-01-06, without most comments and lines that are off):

#define CONFIGURATION_H
#define STRING_VERSION_CONFIG_H __DATE__ " " __TIME__ // build date and time
#define STRING_CONFIG_H_AUTHOR "(CR-10-300)" // Who made the changes.
#define SERIAL_PORT 0
#define BAUDRATE 115200
#define MOTHERBOARD 63
#define EXTRUDERS 1
#define POWER_SUPPLY 1
#define TEMP_SENSOR_0 1
#define TEMP_SENSOR_1 0
#define TEMP_SENSOR_2 0
#define TEMP_SENSOR_BED 1
#define MAX_REDUNDANT_TEMP_SENSOR_DIFF 10
#define TEMP_RESIDENCY_TIME 10  // (seconds)
#define TEMP_HYSTERESIS 3       // (degC) range of +/- temperatures considered "close" to the target one
#define TEMP_WINDOW     1       // (degC) Window around target to start the residency timer x degC early.
#define HEATER_0_MINTEMP 5
#define HEATER_1_MINTEMP 5
#define HEATER_2_MINTEMP 5
#define BED_MINTEMP 5
#define HEATER_0_MAXTEMP 275
#define HEATER_1_MAXTEMP 275
#define HEATER_2_MAXTEMP 275
#define BED_MAXTEMP 150
#define PIDTEMP
#define BANG_MAX 255 // limits current to nozzle while in bang-bang mode; 255=full current
#define PID_MAX 255 // limits current to nozzle while PID is active (see PID_FUNCTIONAL_RANGE below); 255=full current
  #define PID_FUNCTIONAL_RANGE 10 // If the temperature difference between the target temperature and the actual temperature
  #define PID_INTEGRAL_DRIVE_MAX 255  //limit for the integral term
  #define K1 0.95 //smoothing factor within the PID
  #define PID_dT ((OVERSAMPLENR * 8.0)/(F_CPU / 64.0 / 256.0)) //sampling period of the temperature routine
  #define  DEFAULT_Kp 21.73
  #define  DEFAULT_Ki 1.54
  #define  DEFAULT_Kd 76.55
#define MAX_BED_POWER 255 // limits duty cycle to bed; 255=full current
#define PREVENT_DANGEROUS_EXTRUDE
#define PREVENT_LENGTHY_EXTRUDE
#define EXTRUDE_MINTEMP 170
#define EXTRUDE_MAXLENGTH (X_MAX_LENGTH+Y_MAX_LENGTH) //prevent extrusion of very large distances.
#define ENDSTOPPULLUPS // Comment this out (using // at the start of the line) to disable the endstop pullup resistors
  #define ENDSTOPPULLUP_XMAX
  #define ENDSTOPPULLUP_YMAX
  #define ENDSTOPPULLUP_ZMAX
  #define ENDSTOPPULLUP_XMIN
  #define ENDSTOPPULLUP_YMIN
  #define ENDSTOPPULLUP_ZMIN
const bool X_MIN_ENDSTOP_INVERTING = false; // set to true to invert the logic of the endstop.
const bool Y_MIN_ENDSTOP_INVERTING = false; // set to true to invert the logic of the endstop.
const bool Z_MIN_ENDSTOP_INVERTING = false; // set to true to invert the logic of the endstop.
const bool X_MAX_ENDSTOP_INVERTING = false; // set to true to invert the logic of the endstop.
const bool Y_MAX_ENDSTOP_INVERTING = false; // set to true to invert the logic of the endstop.
const bool Z_MAX_ENDSTOP_INVERTING = false; // set to true to invert the logic of the endstop.
#if defined(COREXY) && !defined(DISABLE_MAX_ENDSTOPS)
  #define DISABLE_MAX_ENDSTOPS
#endif
#define X_ENABLE_ON 0
#define Y_ENABLE_ON 0
#define Z_ENABLE_ON 0
#define E_ENABLE_ON 0 // For all extruders
#define DISABLE_X false
#define DISABLE_Y false
#define DISABLE_Z false
#define DISABLE_E false // For all extruders
#define INVERT_X_DIR true    // for Mendel set to false, for Orca set to true
#define INVERT_Y_DIR true    // for Mendel set to true, for Orca set to false
#define INVERT_Z_DIR false     // for Mendel set to false, for Orca set to true
#define INVERT_E0_DIR true   // for direct drive extruder v9 set to true, for geared extruder set to false
#define INVERT_E1_DIR false    // for direct drive extruder v9 set to true, for geared extruder set to false
#define INVERT_E2_DIR false   // for direct drive extruder v9 set to true, for geared extruder set to false
#define X_HOME_DIR -1
#define Y_HOME_DIR -1
#define Z_HOME_DIR -1
#define min_software_endstops true // If true, axis won't move to coordinates less than HOME_POS.
#define max_software_endstops true  // If true, axis won't move to coordinates greater than the defined lengths below.
#define X_MAX_POS 310
#define X_MIN_POS 0
#define Y_MAX_POS 310
#define Y_MIN_POS 0
#define Z_MAX_POS 410
#define Z_MIN_POS 0
#define X_MAX_LENGTH (X_MAX_POS - X_MIN_POS)
#define Y_MAX_LENGTH (Y_MAX_POS - Y_MIN_POS)
#define Z_MAX_LENGTH (Z_MAX_POS - Z_MIN_POS)
#define MANUAL_X_HOME_POS 0
#define MANUAL_Y_HOME_POS 0
#define MANUAL_Z_HOME_POS 0
#define NUM_AXIS 4 // The axis order in all axis related arrays is X, Y, Z, E
#define HOMING_FEEDRATE {50*60, 50*60, 4*60, 0}  // set the homing speeds (mm/min)
#define DEFAULT_AXIS_STEPS_PER_UNIT   {80.000,80.000,400.000,93.00}  // default steps per unit for Ultimaker
#define DEFAULT_MAX_FEEDRATE          {500, 500, 5, 25}    // (mm/sec)
#define DEFAULT_MAX_ACCELERATION      {500,500,100,5000}    // X, Y, Z, E maximum start speed for accelerated moves. E default values are good for skeinforge 40+, for older versions raise them a lot.
#define DEFAULT_ACCELERATION          500    // X, Y, Z and E max acceleration in mm/s^2 for printing moves
#define DEFAULT_RETRACT_ACCELERATION  500   // X, Y, Z and E max acceleration in mm/s^2 for retracts
#define DEFAULT_XYJERK                20.0    // (mm/sec)
#define DEFAULT_ZJERK                 0.4     // (mm/sec)
#define DEFAULT_EJERK                 5.0    // (mm/sec)
#define EEPROM_SETTINGS
#define PLA_PREHEAT_HOTEND_TEMP 185
#define PLA_PREHEAT_HPB_TEMP 0
#define PLA_PREHEAT_FAN_SPEED 255   // Insert Value between 0 and 255
#define ABS_PREHEAT_HOTEND_TEMP 240
#define ABS_PREHEAT_HPB_TEMP 0
#define ABS_PREHEAT_FAN_SPEED 255   // Insert Value between 0 and 255
#define REPRAP_DISCOUNT_FULL_GRAPHIC_SMART_CONTROLLER
 #define DOGLCD
 #define U8GLIB_ST7920
 #define REPRAP_DISCOUNT_SMART_CONTROLLER
 #define ULTIPANEL
 #define NEWPANEL
  #define SDSUPPORT
  #define ULTRA_LCD
    #define LCD_WIDTH 20
    #define LCD_HEIGHT 5
#  define DEFAULT_LCD_CONTRAST 32
#define SOFT_PWM_SCALE 0
#define NUM_SERVOS 1 // Servo index starts with 0 for M280 command
#define SERVO_ENDSTOPS {-1, -1, 0} // Servo index for X, Y, Z. Disable with -1
#define SERVO_ENDSTOP_ANGLES {0,0, 0,0, 125,40} // X,Y,Z Axis Extend and Retract angles
#include "Configuration_adv.h"
#include "thermistortables.h"
